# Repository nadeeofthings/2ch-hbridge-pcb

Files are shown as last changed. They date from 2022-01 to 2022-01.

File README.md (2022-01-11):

# H-Bridge Driver

This is where all the design files for the **H-Bridge Driver** is saved. 
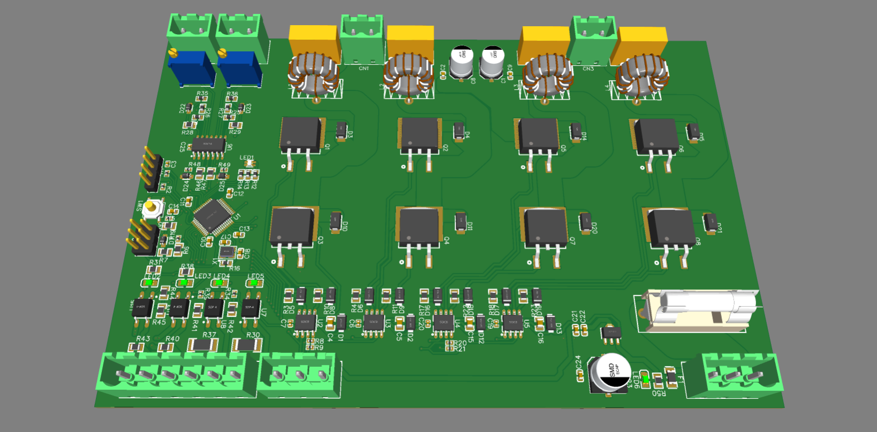
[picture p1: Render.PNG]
Render


# Specifications

 - Channels - 2
 - Input voltage - 12V - 48V
 - Output current - 100A
 - Control input voltage - 12V
 - IO - 2x Analog in, 2x Digital in, 2x Digital out (control) 
 - Output filter type - LC

# Folders

 - **Schematic** - Design schematic
 - **Gerber files** - All the files needed for manufacturing
 - **BOM**- Bill of material for parts order
 - **Firmware** - Embedded software for the microcontroller

# Program 
- Bin file is located in Debug. Use STM32CubeProgrammer and STLink-V2 to program the board through SWD

- UART link is provided to tune the PID parameters and enable outputs.

# ToDo

 - [ ] Finalize firmware
 - [ ] Define UART protocol
 - [ ] Prepare an easy way to calculate inductance and capacitance for the output filter

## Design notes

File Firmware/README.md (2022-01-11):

# H-Bridge driver firmware
Developped using STM32CubeIDE

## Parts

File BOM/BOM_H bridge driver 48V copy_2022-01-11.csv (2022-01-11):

ID | Name | Designator | Footprint | Quantity | Manufacturer Part | Manufacturer | Supplier | Supplier Part | Price
1 | 4.7uF | C1,C8 | CAP-SMD_BD6.3-L6.6-W6.6-FD | 2 | VE-4R7M1H0605-TRO | Lelon | LCSC | C249555 | 0.059
2 | 100nF | C2,C9 | C0603 | 2 | 0603F104M500NT | FH | LCSC | C42998 | 0.002
3 | 100nF | C3,C6,C7,C19,C20,C25 | C0402 | 6 | CC0402JRX7R7BB104 | YAGEO | LCSC | C541464 | 0.002
4 | 1uF | C4,C5,C15,C16 | C0805 | 4 | CL21B105KBFNNNE | SAMSUNG | LCSC | C28323 | 0.008
5 | 220nF | C10,C11,C12,C13,C21 | C0603 | 5 | CL10B224KA8NNNC | SAMSUNG | LCSC | C21120 | 0.005
6 | 1uF | C14,C24 | C0603 | 2 | CL10A105KB8NNNC | SAMSUNG | LCSC | C15849 | 0.005
7 | 20pF | C17,C18 | C0603 | 2 | CL10C200JB8NNNC | SAMSUNG | LCSC | C1648 | 0.004
8 | 4.7uF | C22 | C0603 | 1 | CL10A475KO8NNNC | SAMSUNG | LCSC | C19666 | 0.01
9 | 470uF | C23 | CAP-SMD_BD8.0-L8.3-W8.3-FD | 1 | VT1C471M0810 | ROQANG | LCSC | C141429 | 0.079
10 | XY2500V-B-5.00-2P | CN1,CN3,CN4,CN5 | CONN-TH_2P-P5.00_XY2500V-D-5.00-2P | 4 | XY2500V-B-5.00-2P | -- | LCSC | C505779 | 0.04
11 | XY2500V-B-5.00-6P | CN2 | CONN-TH_6P-P5.00_XY2500V-D-5.00-6P | 1 | XY2500V-B-5.00-6P | -- | LCSC | C505783 | 0.101
12 | XY2500V-B-5.00-3P | CN6,CN7 | CONN-TH_3P-P5.00_XY2500V-D-5.00-3P | 2 | XY2500V-B-5.00-3P | -- | LCSC | C505780 | 0.059
13 | 1N5819W | D1,D2,D5,D6,D8,D9,D12,D13,D16,D17,D18,D19 | SOD-123F_L2.8-W1.8-LS3.7-RD | 12 | 1N5819W | Shandong Jingdao Microelectronics | LCSC | C169540 | 0.022
14 | SS36 | D3,D4,D10,D11,D14,D15,D20,D21 | SMA_L4.3-W2.6-LS5.2-RD | 8 | SS36 | MDD | LCSC | C16015 | 0.055
15 | ZLLS410TA | D7 | SOD-323_L1.8-W1.3-LS2.5-RD | 1 | ZLLS410TA | Diodes Incorporated | LCSC | C177096 | 0.217
16 | BZT52C3V3S_C173439 | D22,D23,D24,D25 | SOD-323_L1.8-W1.3-LS2.5-RD | 4 | BZT52C3V3S | (MDD) Jiangsu Yutai Elec | LCSC | C173439 | 0.016
17 | nSMD050-13.2V | F1 | F1206 | 1 | nSMD050-13.2V | TECHFUSE | LCSC | C70074 | 0.035
18 | 64600001003 | FH1 | 64600001003 | 1 | 64600001003 | Littelfuse | LCSC | C206887 | 0.61
19 | HDR-M-2.54_1x4 | J1 | HDR-M-2.54_1X4 | 1 |  |  | LCSC | C124378 | 0.029
20 | HDR-M-2.54_2x3 | J2 | HDR-M-2.54_2X3 | 1 |  |  | LCSC | C65114 | 0.028
21 | 4.7u | L1,L2,L3,L4 | IND-TH_L14.0-W6.5-P8.00-D0.6 | 4
22 | TJ-S1615SW6TGLCCSRGB-A5 | LED1 | LED-ARRAY-SMD_4P-L1.6-W1.5-BL-FD | 1 | TJ-S1615SW6TGLCCSRGB-A5 | TOGIALED | LCSC | C273611 | 0.096
23 | 17-21SURC/S530-A3/TR8 | LED2,LED3,LED4,LED5,LED6 | LED0805-R-RD | 5 | 17-21SURC/S530-A3/TR8 | EVERLIGHT | LCSC | C72037 | 0.015
24 | STB15810 | Q1,Q2,Q3,Q4,Q5,Q6,Q7,Q8 | D2PAK_L10.2-W9.0-P5.08-LS16.9-BR | 8 | STB15810 | ST(意法半导体) | LCSC | C620154
25 | 10K | R1,R2,R8,R9,R15,R19,R20,R21,R34,R39,R48,R49 | R0402 | 12 | TC0225B1002TCE | Uniroyal Elec | LCSC | C84351 | 0.068
26 | 27 | R3,R4,R10,R11,R17,R18,R22,R23 | R0805 | 8 | 0805W8F270JT5E | UniOhm | LCSC | C17594 | 0.003
27 | 1.5K | R5 | R0805 | 1 | 0805W8F1501T5E | UniOhm | LCSC | C4310 | 0.002
28 | 20 | R6,R7 | R0805 | 2 | 0805W8F200JT5E | UniOhm | LCSC | C17544 | 0.002
29 | 100 | R12,R13,R14 | R0603 | 3 | TC0325B1000T5E | UniOhm | LCSC | C54021 | 0.041
30 | 2.1M | R16 | R0603 | 1 | 0603WAF2104T5E | Uniroyal Elec | LCSC | C422961 | 0.002
31 | 820K | R24,R25,R26,R27 | R0603 | 4 | 0603WAF8203T5E | UniOhm | LCSC | C23252 | 0.001
32 | 47K | R28,R29 | R0805 | 2 | TC0525B4702T5E | Uniroyal Elec | LCSC | C108049 | 0.039
33 | 1.4K | R30,R37 | R2010 | 2 | 2010W2F1401T4S | UniOhm | LCSC | C54203 | 0.013
34 | 120 | R31,R38,R41,R42,R44,R45 | R0805 | 6 | 0603WAF1300T5E | UniOhm | LCSC | C22796 | 0.001
35 | 100K | R32,R33 | RES-ADJ-TH_3P-L9.5-W4.9-P2.50-L_3296W | 2 | 3296W-1-104 | Chengdu Guosheng Tech | LCSC | C118963 | 0.172
36 | 24K | R35,R36 | R0603 | 2 | 0603WAF2492T5E | UniOhm | LCSC | C25962 | 0.002
37 | 56K | R40,R43 | R0805 | 2 | 0805W8F5602T5E | UniOhm | LCSC | C17756 | 0.003
38 | 20K | R46,R47 | R0805 | 2 | TC0525B2002T5E | Uniroyal Elec | LCSC | C55865 | 0.039
39 | 560 | R50 | R0805 | 1 | 0805W8F5600T5E | UniOhm | LCSC | C28636 | 0.003
40 | TS-1187A-B-A-B | SW1 | SW-SMD_4P-L5.1-W5.1-P3.70-LS6.5-2 | 1 | TS-1187A-B-A-B | XKB Enterprise | LCSC | C318884 | 0.014
41 | STM32F103C8T6 | U1 | LQFP-48_L7.0-W7.0-P0.50-LS9.0-BL | 1 | STM32F103C8T6 | STMicroelectronics | LCSC | C8734 | 10.454
42 | IR2104STRPBF | U2,U3,U4,U5 | SOIC-8_L4.9-W3.9-P1.27-LS6.0-BL | 4 | IR2104STRPBF | IR | LCSC | C2960 | 1.328
43 | TLP185(GB-TPL,SE(T | U7,U8,U13,U15 | SOP-4_L4.4-W4.0-P2.54-LS7.0-BR | 4 | TLP185(GB-TPL,SE(T | TOSHIBA | LCSC | C7240 | 0.3
44 | 220nF | U9,U10,U11,U12 | CAP-TH_L13.0-W5.0-P10.00-D0.6 | 4 | C232E224J4SC000 | XIAMEN FARATRONIC | LCSC | C328906 | 0.154
45 | AMS1117-3.3 | U14 | SOT-89-3_L4.5-W2.5-P1.50-LS4.2-TR | 1 | AMS1117-3.3 | Slkor(SLKORMICRO Elec.) | LCSC | C880752 | 0.112
46 | 16MHz | X1 | OSC-SMD_4P-L3.2-W2.5-BL | 1 | X322516MRB4SI | YXC | LCSC | C70562 | 0.09
47 | LM324ADR | U6 | SOIC-14_L8.7-W3.9-P1.27-LS6.0-BL | 1 | LM324ADR | TI | LCSC | C66406 | 0.192

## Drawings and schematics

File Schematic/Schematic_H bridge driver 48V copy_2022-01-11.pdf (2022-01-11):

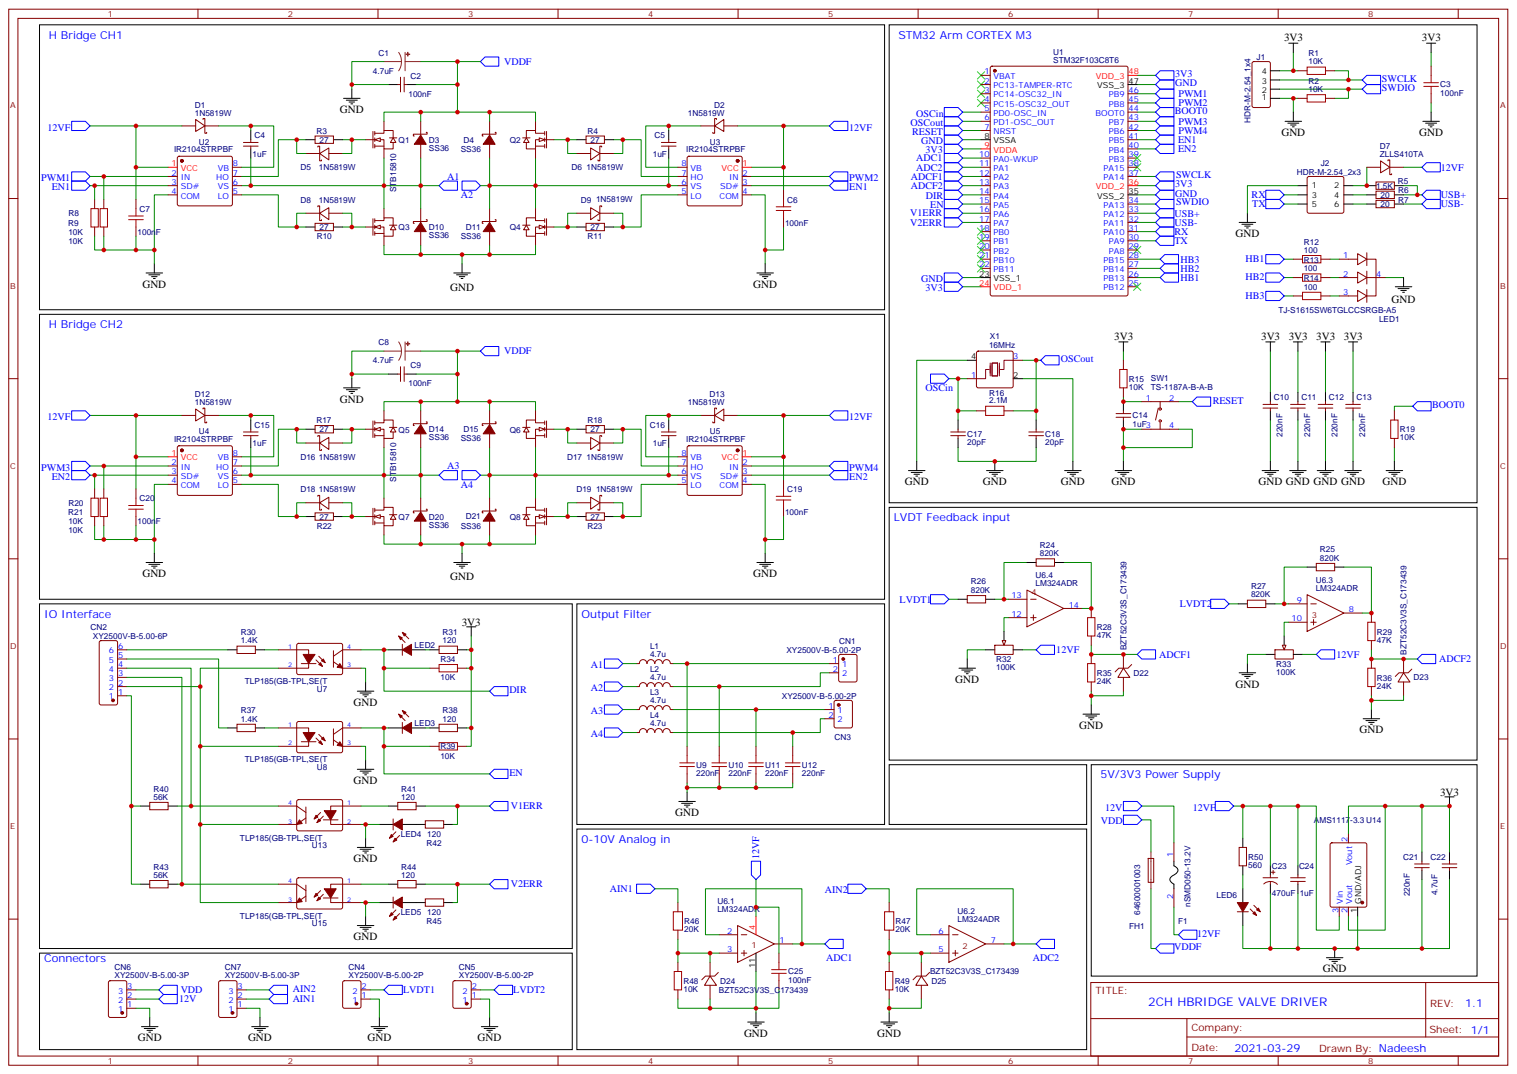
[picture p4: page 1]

GND GND GND GND²²⁰nF

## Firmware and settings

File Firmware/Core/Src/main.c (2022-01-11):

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
/* Includes ------------------------------------------------------------------*/
#include "main.h"
#include "usb_device.h"

/* USER CODE BEGIN Includes */
#include "usbd_cdc_if.h"
#include "string.h"
#include "pid_controller.h"
/* USER CODE END Includes */

/* USER CODE BEGIN PD */
#define AVERAGE_LENGTH 5
/* USER CODE END PD */

ADC_HandleTypeDef hadc1;
ADC_HandleTypeDef hadc2;

TIM_HandleTypeDef htim4;

/* USER CODE BEGIN PV */
uint32_t currentMillis;
uint32_t previousMillis = 0;
uint32_t PIDInterval = 20;

extern USBD_HandleTypeDef hUsbDeviceFS;
uint8_t dataRxToggle;
uint8_t userSerialRXBuffer[APP_RX_DATA_SIZE];
uint8_t dataRxFlag = 0;

uint16_t ADC_Value[4] = { 0 };

uint16_t setPoint1MovingAverage[AVERAGE_LENGTH] = { 0 };
uint16_t feedback1MovingAverage[AVERAGE_LENGTH] = { 0 };
uint16_t setPoint2MovingAverage[AVERAGE_LENGTH] = { 0 };
uint16_t feedback2MovingAverage[AVERAGE_LENGTH] = { 0 };
uint8_t setPoint1Pos = 0;
uint8_t setPoint2Pos = 0;
uint8_t feedback1Pos = 0;
uint8_t feedback2Pos = 0;
uint32_t setPoint1Sum = 0;
uint32_t setPoint2Sum = 0;
uint32_t feedback1Sum = 0;
uint32_t feedback2Sum = 0;
uint16_t setPoint1Avg = 0;
uint16_t setPoint2Avg = 0;
uint16_t feedback1Avg = 0;
uint16_t feedback2Avg = 0;
int setPoint1Map = 0;
int setPoint2Map = 0;
int feedback1Map = 0;
int feedback2Map = 0;

float kP1 = 0.001;
float kI1 = 0;
float kD1 = 0;

float kP2 = 0.001;
float kI2 = 0;
float kD2 = 0;

float percentage = 0;
uint8_t displayToggle = 0;

float PID1_out;
float PID2_out;

PIDControl PID1;
PIDControl PID2;


/* USER CODE END PV */

void SystemClock_Config(void);
static void MX_GPIO_Init(void);
static void MX_TIM4_Init(void);
static void MX_ADC1_Init(void);
static void MX_ADC2_Init(void);
/* USER CODE BEGIN PFP */
uint16_t user_get_adc1(void);
uint16_t user_get_adc2(void);
uint16_t movingAvg(uint16_t *ptrArrNumbers, uint32_t *ptrSum, uint8_t *pos,
		uint8_t len, uint16_t nextNum);
int user_MAP(int x, int in_min, int in_max, int out_min, int out_max);
void processRx(PIDControl *pid1, PIDControl *pid2);
/* USER CODE END PFP */

/**
  * @brief  The application entry point.
  * @retval int
  */
int main(void)
{
  /* MCU Configuration--------------------------------------------------------*/

  /* Reset of all peripherals, Initializes the Flash interface and the Systick. */
  HAL_Init();

  /* Configure the system clock */
  SystemClock_Config();

  /* Initialize all configured peripherals */
  MX_GPIO_Init();
  MX_TIM4_Init();
  MX_ADC1_Init();
  MX_USB_DEVICE_Init();
  MX_ADC2_Init();
  /* USER CODE BEGIN 2 */
	PIDInit(&PID1, kP1, kI1, kD1, 0.020, -8000, 8000, AUTOMATIC, DIRECT);
	PIDInit(&PID2, kP2, kI2, kD2, 0.020, -8000, 8000, AUTOMATIC, DIRECT);
	HAL_TIM_PWM_Start(&htim4, TIM_CHANNEL_1);
	HAL_TIM_PWM_Start(&htim4, TIM_CHANNEL_2);
	HAL_TIM_PWM_Start(&htim4, TIM_CHANNEL_3);
	HAL_TIM_PWM_Start(&htim4, TIM_CHANNEL_4);


  /* USER CODE END 2 */

  /* Infinite loop */
  /* USER CODE BEGIN WHILE */
	while (1) {
		currentMillis = HAL_GetTick();
		if (currentMillis - previousMillis >= PIDInterval) { //start timed event
			previousMillis = currentMillis;

			// Get ADC value
			for (uint8_t i = 0; i < 2; i++) {
				//Store ADC values of channel 1, 2 and 3 respectively
				ADC_Value[i] = user_get_adc1();
			}
			for (uint8_t i = 2; i < 4; i++) {
				//Store ADC values of channel 1, 2 and 3 respectively
				ADC_Value[i] = user_get_adc2();
			}

			setPoint1Map = user_MAP(movingAvg(setPoint1MovingAverage, &setPoint1Sum,
					&setPoint1Pos, AVERAGE_LENGTH, ADC_Value[0]), 0, 2800, -7000, 7000);
			feedback1Map = user_MAP(movingAvg(feedback1MovingAverage, &feedback1Sum,
								&feedback1Pos, AVERAGE_LENGTH, ADC_Value[1]), 700, 1900, -8000, 8000);


			setPoint2Map = user_MAP(movingAvg(setPoint2MovingAverage, &setPoint2Sum,
								&setPoint2Pos, AVERAGE_LENGTH, ADC_Value[2]), 0, 2800, -7000, 7000);
			feedback2Map = user_MAP(movingAvg(feedback2MovingAverage, &feedback2Sum,
								&feedback2Pos, AVERAGE_LENGTH, ADC_Value[3]), 700, 1900, -8000, 8000);

			//setPoint2Map = setPoint1Map;

			PIDSetpointSet(&PID1, setPoint1Map);
			PIDInputSet(&PID1, feedback1Map);

			PIDSetpointSet(&PID2, setPoint2Map);
			PIDInputSet(&PID2, feedback2Map);



			if(!HAL_GPIO_ReadPin(MASTER_EN_GPIO_Port, MASTER_EN_Pin)){

				PIDModeSet(&PID1, AUTOMATIC);
				PIDModeSet(&PID2, AUTOMATIC);

				PIDCompute(&PID1);
				PIDCompute(&PID2);

				PID1_out = (PIDOutputGet(&PID1) * percentage);
				PID2_out = (PIDOutputGet(&PID2) * percentage);

				HAL_GPIO_WritePin (GPIOB, EN2_Pin, 1);
				HAL_GPIO_WritePin (GPIOB, EN1_Pin, 1);
			}else {

				PIDModeSet(&PID1, MANUAL);
				PIDModeSet(&PID2, MANUAL);

				PIDCompute(&PID1);
				PIDCompute(&PID2);

				PID1_out = 0;
				PID2_out = 0;

				HAL_GPIO_WritePin (GPIOB, EN2_Pin, 0);
				HAL_GPIO_WritePin (GPIOB, EN1_Pin, 0);
			}

			if (PID1_out >= 0) {
				__HAL_TIM_SET_COMPARE(&htim4, TIM_CHANNEL_3, PID1_out);
				__HAL_TIM_SET_COMPARE(&htim4, TIM_CHANNEL_4, 0);
			      }
			else if (PID1_out < 0) {
			        __HAL_TIM_SET_COMPARE(&htim4, TIM_CHANNEL_3, 0);
			        __HAL_TIM_SET_COMPARE(&htim4, TIM_CHANNEL_4, abs(PID1_out));
		    }
			if (PID2_out >= 0) {
				__HAL_TIM_SET_COMPARE(&htim4, TIM_CHANNEL_1, PID2_out);
				__HAL_TIM_SET_COMPARE(&htim4, TIM_CHANNEL_2, 0);
			      }
			else if (PID2_out < 0) {
			        __HAL_TIM_SET_COMPARE(&htim4, TIM_CHANNEL_1, 0);
			        __HAL_TIM_SET_COMPARE(&htim4, TIM_CHANNEL_2, abs(PID2_out));
		    }


			char buffer[40];
			if(displayToggle == 1){
				sprintf(buffer, "%d , %d , %d , %d\r\n", setPoint2Map, feedback2Map, (int)PID2_out, (displayToggle<<7));
			}else{
				sprintf(buffer, "%d , %d , %d , %d\r\n", setPoint1Map, feedback1Map, (int)PID1_out, displayToggle);
			}
			CDC_Transmit_FS((uint8_t*) buffer, strlen(buffer));
			//USBD_CDC_SetRxBuffer(&hUsbDeviceFS, serialRXBuffer);
			//CDC_Transmit_FS(userSerialRXBuffer, strlen(userSerialRXBuffer));
			processRx(&PID1, &PID2);

		}
    /* USER CODE END WHILE */

    /* USER CODE BEGIN 3 */
	}
  /* USER CODE END 3 */
}

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
/* USER CODE BEGIN 4 */
uint16_t user_get_adc1() {
	//Turn ADC1 on
	HAL_ADC_Start(&hadc1);
	//Wait for ADC conversion to complete, the timeout is 100ms
	HAL_ADC_PollForConversion(&hadc1, 100);
	//Judge whether ADC conversion is successful
	if (HAL_IS_BIT_SET(HAL_ADC_GetState(&hadc1), HAL_ADC_STATE_REG_EOC)) {
		//Read value
		return HAL_ADC_GetValue(&hadc1);
	}
	return 0;
}
uint16_t user_get_adc2() {
	//Turn ADC1 on
	HAL_ADC_Start(&hadc2);
	//Wait for ADC conversion to complete, the timeout is 100ms
	HAL_ADC_PollForConversion(&hadc2, 100);
	//Judge whether ADC conversion is successful
	if (HAL_IS_BIT_SET(HAL_ADC_GetState(&hadc2), HAL_ADC_STATE_REG_EOC)) {
		//Read value
		return HAL_ADC_GetValue(&hadc2);
	}
	return 0;
}
uint16_t movingAvg(uint16_t *ptrArrNumbers, uint32_t *ptrSum, uint8_t *pos,
		uint8_t len, uint16_t nextNum) {

	//Subtract the oldest number from the prev sum, add the new number
	*ptrSum = *ptrSum - ptrArrNumbers[*pos] + nextNum;
	//Assign the nextNum to the position in the array
	ptrArrNumbers[*pos] = nextNum;
	//increment the position
	*pos = *pos + 1;
	if (*pos >= len) {
		*pos = 0;
	}
	//return the average
	return *ptrSum / len;
}

void processRx(PIDControl *pid1, PIDControl *pid2) {
	if (dataRxFlag != dataRxToggle) {
		float kP1, kI1, kD1;
		// Returns first token
		char *token = strtok(userSerialRXBuffer, ",");
		if(token[0] == 'L'){
			token = strtok(NULL, ",");
			kP1 = (float)atof(token);
			token = strtok(NULL, ",");
			kI1 = (float)atof(token);
			token = strtok(NULL, ",");
			kD1 = (float)atof(token);

			if(kP1 >= 0 && kD1 >= 0 && kI1 >= 0){
				PIDTuningsSet(pid1, kP1, kI1, kD1);
			}
			HAL_GPIO_TogglePin (GPIOB, STS_R_Pin);
		}else if(token[0] == 'R'){
			token = strtok(NULL, ",");
			kP1 = (float)atof(token);
			token = strtok(NULL, ",");
			kI1 = (float)atof(token);
			token = strtok(NULL, ",");
			kD1 = (float)atof(token);

			if(kP1 >= 0 && kD1 >= 0 && kI1 >= 0){
				PIDTuningsSet(pid2, kP1, kI1, kD1);
		}
			HAL_GPIO_TogglePin (GPIOB, STS_G_Pin);
		}else if(token[0] == 'G'){
			token = strtok(NULL, ",");
			percentage = (float)atof(token);
			HAL_GPIO_TogglePin (GPIOB, STS_B_Pin);
		}else if(token[0] == 'D'){
			token = strtok(NULL, ",");
			if(token[0] == 'L'){
				displayToggle = 0;
			}else if(token[0] == 'R'){
				displayToggle = 1;
			}
			HAL_GPIO_TogglePin (GPIOB, STS_B_Pin);
		}
		dataRxFlag = dataRxToggle;
	}

}
int user_MAP(int x, int in_min, int in_max, int out_min, int out_max){

	return (x - in_min) * (out_max - out_min) / (in_max - in_min) + out_min;
}
/* USER CODE END 4 */
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


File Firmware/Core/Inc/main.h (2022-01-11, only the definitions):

#define MASTER_DIR_Pin GPIO_PIN_4
#define MASTER_DIR_GPIO_Port GPIOA
#define MASTER_EN_Pin GPIO_PIN_5
#define MASTER_EN_GPIO_Port GPIOA
#define STS_R_Pin GPIO_PIN_13
#define STS_R_GPIO_Port GPIOB
#define STS_G_Pin GPIO_PIN_14
#define STS_G_GPIO_Port GPIOB
#define STS_B_Pin GPIO_PIN_15
#define STS_B_GPIO_Port GPIOB
#define EN2_Pin GPIO_PIN_4
#define EN2_GPIO_Port GPIOB
#define EN1_Pin GPIO_PIN_5
#define EN1_GPIO_Port GPIOB

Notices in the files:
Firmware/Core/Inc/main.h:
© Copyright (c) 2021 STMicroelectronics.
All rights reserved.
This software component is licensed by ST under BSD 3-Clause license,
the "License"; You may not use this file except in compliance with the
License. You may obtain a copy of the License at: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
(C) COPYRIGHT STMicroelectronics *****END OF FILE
